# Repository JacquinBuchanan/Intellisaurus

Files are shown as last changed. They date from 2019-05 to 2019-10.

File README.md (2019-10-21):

# Intellisaurus
walking robot kit

## Assembly Videos

[Intellisaurus - Part 1 - Framing](https://www.youtube.com/watch?v=A2P9gOie0s8)

[Intellisaurus - Part 2 - Custom Cables](https://www.youtube.com/watch?v=bgMKRhBEzlM&t=16s)

[Intellisaurus - Part 3 - More Framing](https://www.youtube.com/watch?v=AXAqG9Cf0UA&t=1474s)

[Intellisaurus - Part 4 - Wiring](https://www.youtube.com/watch?v=rhYsjQ5Yf_Y)

[Intellisaurus - Part 5 - Leg Assembly](https://www.youtube.com/watch?v=X2EEQunwOJA)

[Intellisaurus - Part 6 - Shell](https://www.youtube.com/watch?v=MMXVz9HQz3Y)

[Intellisaurus - Part 7 - Installing AI Kit](https://www.youtube.com/watch?v=gh2QlOyxaBA)

## Parts List
Frame Parts Laser cut from 3mm acrylic

3D printed Leg Parts

3D printed Shell parts

1 - MG90s Servo

10 - MG966s Servos https://www.amazon.com/gp/product/B07BVR816V

Arduino Nano https://www.amazon.com/gp/product/B07G99NNXL

Servo Controller board PCA9685 https://www.amazon.com/gp/product/B07BRS249H/

Sharp Distance Sensor 10 cm ( GP2Y0D810Z0F) https://www.adafruit.com/product/1927

Battery Holder for 2 18650 https://www.amazon.com/gp/product/B06XT1DM74

5 volt @ 3 Amp Voltage Regulator (for Raspberry PI) https://www.amazon.com/gp/product/B07PLSYX9G

5 volt @ 3 Amp Voltage Regulator (for Servos) https://www.amazon.com/dp/B07QX562Z5

On/Off Switch https://www.amazon.com/gp/product/B07B9RPLZD

IR Remote control with Sensor https://www.amazon.com/gp/product/B01EE4VXS0

MPU6050 Sensor https://www.amazon.com/gp/product/B00LP25V1A

3" Speaker https://www.adafruit.com/product/1314

Raspberry Pi Zero W https://www.adafruit.com/product/3708

ReSpeaker w/ microphone Array https://www.amazon.com/gp/product/B07CXSW6LB

Raspberry Pi Camera V2 https://www.amazon.com/gp/product/B01ER2SKFS

Raspberry Pi Camera to Pi Zero Cable https://www.adafruit.com/product/3157

Groove Connector https://www.amazon.com/gp/product/B01CNZ9RJO

USB connector https://www.amazon.com/gp/product/B00OK8ELNA

Servo Label Stickers

Female to Female jumper wires https://www.amazon.com/gp/product/B07GN731BK

M2 x 25mm bolt - 2

M3 x 35mm bolt  - 1

M2 x 6mm bolt - 37 https://www.amazon.com/gp/product/B0762HR8DQ

M2 x 12 mm bolt - 33 https://www.amazon.com/gp/product/B0762K9RP5

M3 x 10mm bolt - 52 https://www.amazon.com/gp/product/B012TBMGUE

M3 Nylon nuts - 61 https://www.amazon.com/gp/product/B0129BDGW6

M2 nuts - 38 https://www.amazon.com/gp/product/B07D35C66V

M2 x 6mm Nylon hex standoffs - 10 https://www.amazon.com/gp/product/B07GCXFVB1

M3 x 50mm bolt - 6 https://www.amazon.com/gp/product/B012TE1JDG

m2 x 8mm self tapping screws - 2( to mount camera) https://www.amazon.com/gp/product/B01M0P01I5

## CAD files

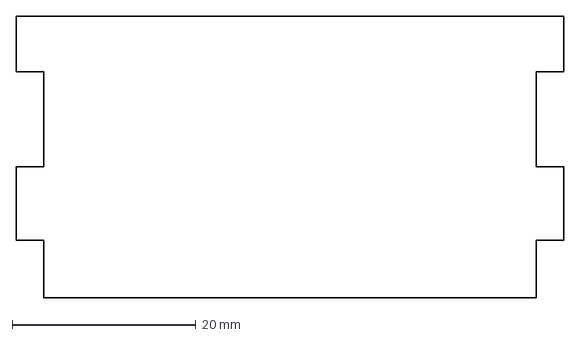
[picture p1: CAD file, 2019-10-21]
Frame DXFs/Frame Plate 9.dxf
59.6 x 30.6 mm

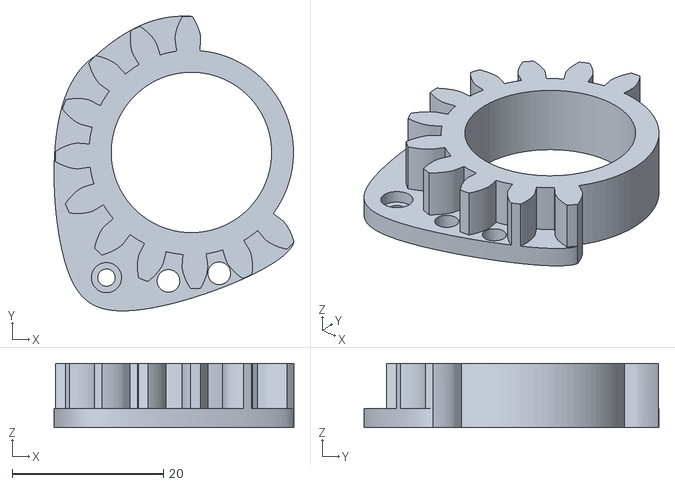
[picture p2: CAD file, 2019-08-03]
Legs STLs/FR Primary Gear.stl
31.7 x 39.0 x 8.50

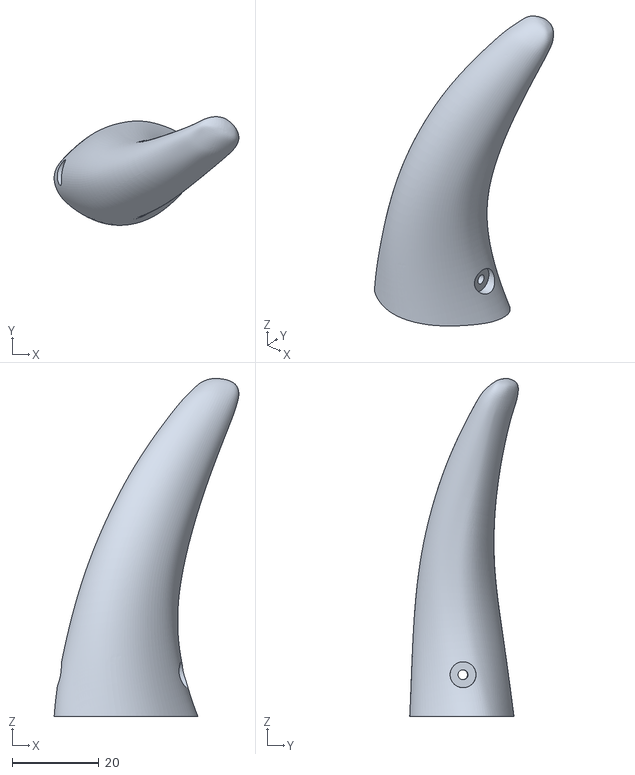
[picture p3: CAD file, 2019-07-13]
Shell STLs/Tail 3.stl
42.7 x 25.1 x 78.1

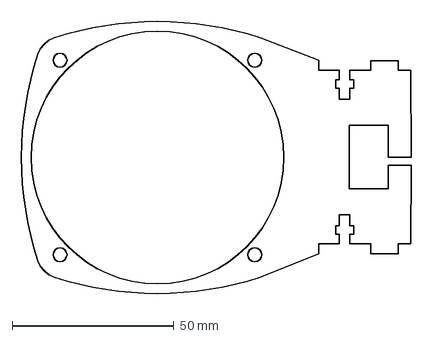
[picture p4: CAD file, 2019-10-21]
Frame DXFs/Frame Plate 4.dxf
122.0 x 87.4 mm

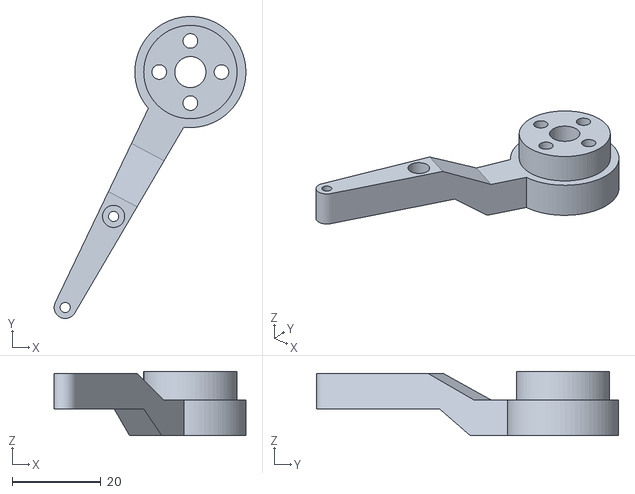
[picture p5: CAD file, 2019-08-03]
Legs STLs/FL Leg 1.stl
43.2 x 68.0 x 14.5

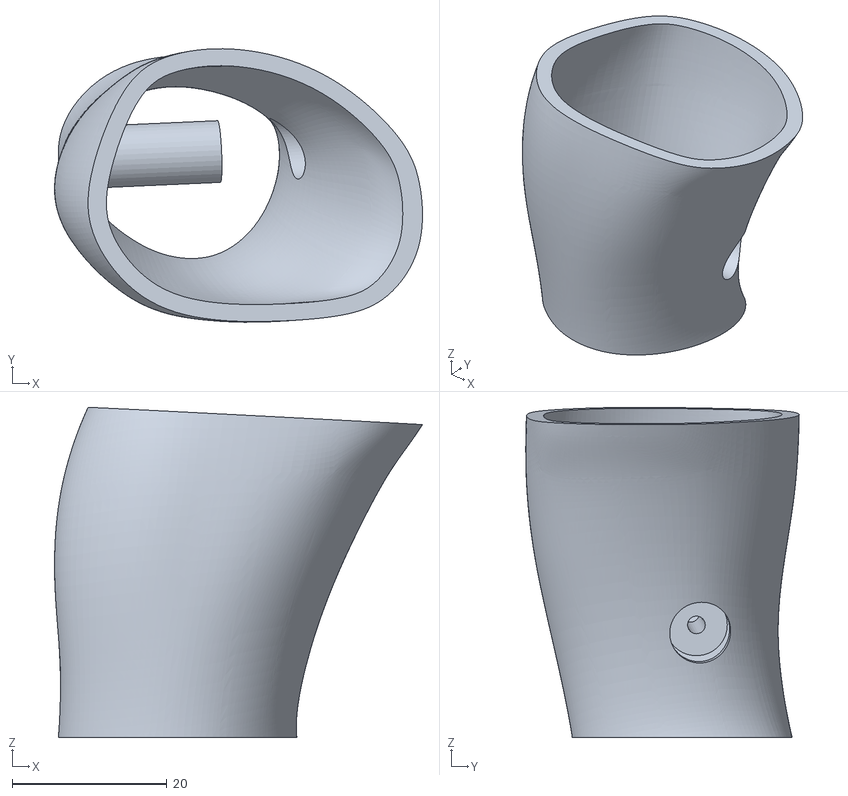
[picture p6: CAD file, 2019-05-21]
Shell STLs/BR Leg Lower.stl
47.6 x 35.4 x 42.7

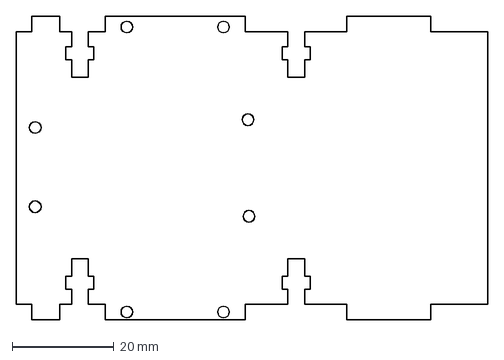
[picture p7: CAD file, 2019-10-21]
Frame DXFs/Frame Plate 5.dxf
92.7 x 59.6 mm

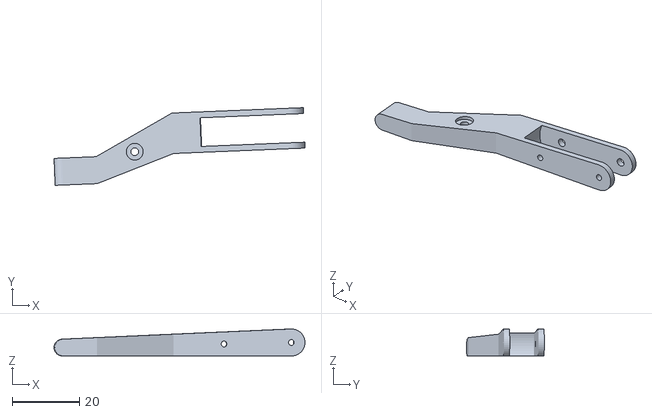
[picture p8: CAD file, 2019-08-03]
Legs STLs/FL Leg 3.stl
74.4 x 23.0 x 8.00

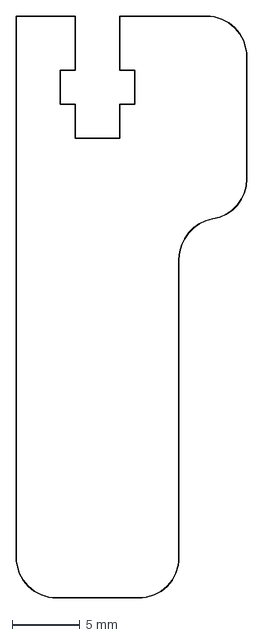
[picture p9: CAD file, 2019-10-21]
Frame DXFs/Frame Side Support.dxf
17.0 x 42.9 mm

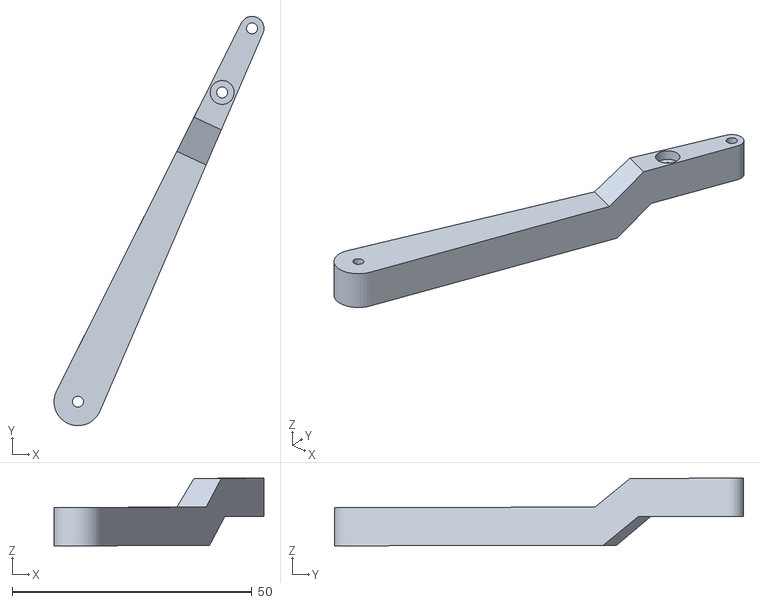
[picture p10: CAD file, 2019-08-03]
Legs STLs/BR Leg 2.stl
43.8 x 85.4 x 14.1

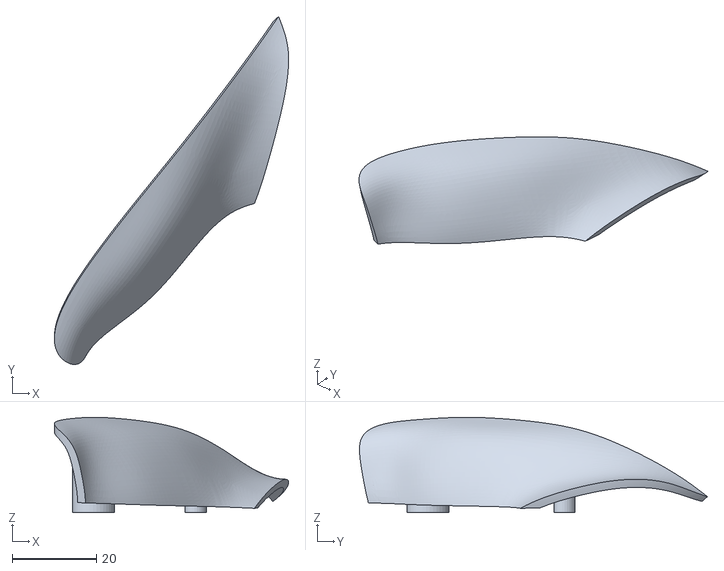
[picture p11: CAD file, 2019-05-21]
Shell STLs/FR Leg Upper 1.stl
55.7 x 82.7 x 22.6

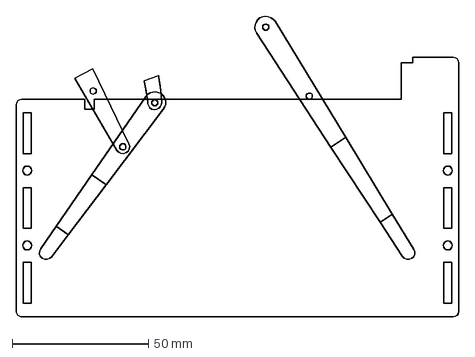
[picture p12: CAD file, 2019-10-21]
Frame DXFs/Stand Left Frame.dxf
162.7 x 110.5 mm

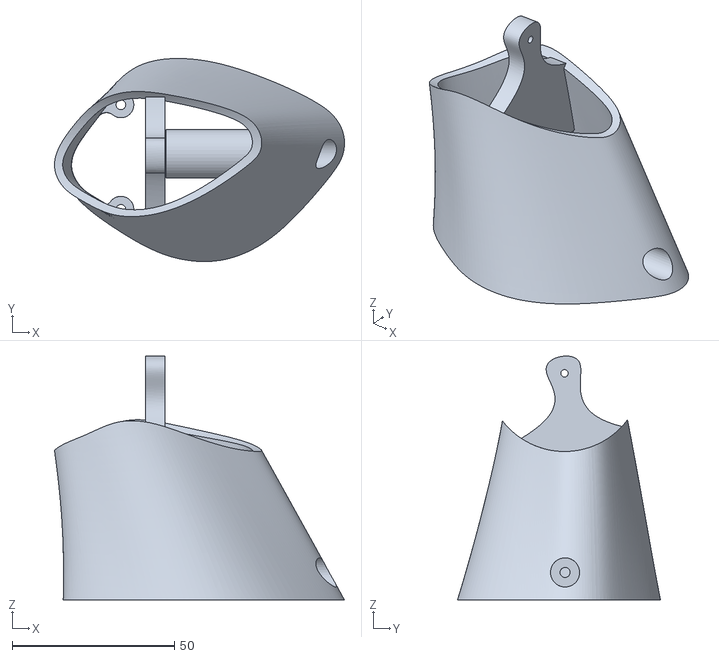
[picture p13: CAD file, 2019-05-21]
Shell STLs/Tail 1.stl
89.5 x 62.7 x 75.3

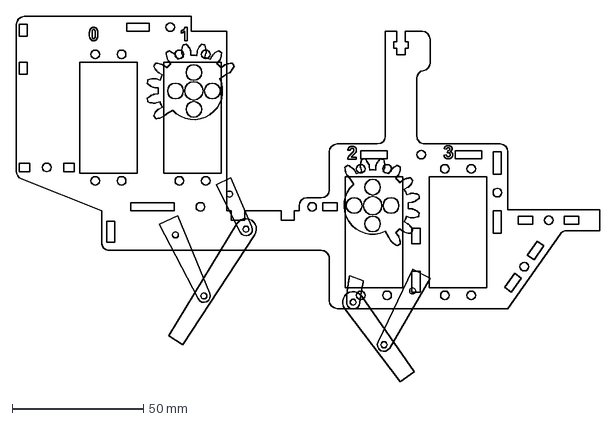
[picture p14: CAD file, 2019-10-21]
Frame DXFs/Right Body Frame.dxf
221.8 x 138.9 mm

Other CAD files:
Shell STLs/BL Leg Lower.stl
Legs STLs/BL Leg 2.stl
Legs STLs/BR Primary Gear.stl
Shell STLs/BL Leg Upper 2.stl
Frame DXFs/Frame Plate 1.dxf
Frame DXFs/Frame Plate 10.dxf
Frame DXFs/Frame Plate 2.dxf
Frame DXFs/Frame Plate 3.dxf
Frame DXFs/Frame Plate 6.dxf
Frame DXFs/Frame Plate 7.dxf
Frame DXFs/Frame Plate 8.dxf
Frame DXFs/Left Body Frame.dxf
Frame DXFs/Neck Holder Frame 2.dxf
Frame DXFs/Neck Holder Frame.dxf
Frame DXFs/Stand Cross Frame.dxf
Frame DXFs/Stand Right Frame.dxf
Legs STLs/Arduino Holder.stl
Legs STLs/BL Leg 1.stl
Legs STLs/BL Leg 3.stl
Legs STLs/BL Primary Gear 2.stl
Legs STLs/BL Primary Gear.stl
Legs STLs/BL Secondary Gear.stl
Legs STLs/BL Washer.stl
Legs STLs/BR Leg 1.stl
Legs STLs/BR Leg 3.stl
Legs STLs/BR Primary Gear 2.stl
Legs STLs/BR Secondary Gear.stl
Legs STLs/BR Washer.stl
Legs STLs/FL Leg 2.stl
Legs STLs/FL Primary Gear 2.stl
Legs STLs/FL Primary Gear.stl
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

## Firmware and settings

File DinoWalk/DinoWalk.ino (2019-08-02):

/***************************************************
     Quadropewd Walking Dinosour Robot

     copyright Jacquin Buchanan 2018
****************************************************/
#include "DinoRemoteControl.h"
#include <MPU6050_tockn.h>
#include <Wire.h>
#include <EEPROM.h>
#include <Adafruit_PWMServoDriver.h>

// called this way, it uses the default address 0x40
Adafruit_PWMServoDriver pwm = Adafruit_PWMServoDriver();
MPU6050 mpu6050(Wire);


// Define IR distance sensor model and input pin:
#define IRPin 3

// Choose the IR protocol of your remote. this isi the one shipped in the kit
CNec IRLremote;

#define MIN_PULSE_WIDTH 450
#define MAX_PULSE_WIDTH 2350
#define FREQUENCY 50

#define BACK_LEG_L1 86
#define BACK_LEG_L2 68
#define BACK_LEG_HIP_OFFSET_ANGLE  65.1
#define BACK_LEG_KNEE_OFFSET_ANGLE (-57.2)

#define FRONT_LEG_L1 60
#define FRONT_LEG_L2 48
#define FRONT_LEG_HIP_OFFSET_ANGLE  62
#define FRONT_LEG_KNEE_OFFSET_ANGLE (-64.1)

#define BACK_TO_FRONT_HIP_DIF 43.6

//These are the amount each motor gear is off from true because of the 7 degree gear size;
// these are stored in the EPROM
float MotorBuildOffsets[10] = {0.0, 0.0 , 0.0 , 0.0 , 0.0 , 0.0, 0.0, 0.0, 0.0, 0.0};
int CurrentMotorAdjusting = -1;

// The distance off the ground to hip of a normal walk
#define NORMAL_WALK_HEIGHT 98

// The distance off the ground to raise foot of a normal walk
float FootRaise[5] = {20.0, 20.0, 15.0, 10.0, 10.0};

#define MIN_FOOT_HEIGHT 70
#define MAX_FOOT_HEIGHT 100

#define MIN_FOOT_X -40
#define MAX_FOOT_X 40
#define NORMAL_STEP_LENGTH 55

#define FRONT_STEP_OFFSET_FROM_HIP_FORWARDS 0
#define BACK_STEP_OFFSET_FROM_HIP_FORWARDS 10

#define FRONT_STEP_OFFSET_FROM_HIP_BACKWARDS 15
#define BACK_STEP_OFFSET_FROM_HIP_BACKWARDS 15

int speedIndex = 0;
float StepTime[5] = {1000, 700, 500, 400, 400}; //the time for one foot step forward. (i.e. 1/4 the entire walk cycle)
float RightSideStepLength = NORMAL_STEP_LENGTH; // mm distance that each foot moves forward. NOTE this is differnt for left and right to allow turning.
float LeftSideStepLength = NORMAL_STEP_LENGTH; // mm distance that each foot moves forward. NOTE this is differnt for left and right to allow turning.

boolean leftBackwards = false;
boolean rightBackwards = false;

//four phases to a walk. One for each foot moving forward
// 0 is back right,
// 1 is front right
// 2 is back left
// 3 is front left
int walkphase = 0;

int walkPhaseIndex = 0;

int backwardsWalkPhases[4] = {1,0,3,2};

//The start time for each foots phase
unsigned long  phaseStartTime[4];
float PhaseStartFootXPos[4];
float FootXPos[4] = {0, 0, 0, 0};
float FootYPos[4] = {NORMAL_WALK_HEIGHT, NORMAL_WALK_HEIGHT, NORMAL_WALK_HEIGHT, NORMAL_WALK_HEIGHT};
boolean FootStanding[4];


//mode is used to decide what the motors are doing
// 0 is tweaking motor offsets
// 1 is standing still
// 2 is slow walking
// 3 is starting to walk, (i.e. shift weight)
// 4 is jogging
uint8_t mode;


//PID balancing variables
double last_error_LR = 0.0;
double Kp_LR = 0.02;//0.05;
double Kd_LR = 0.17;//0.17;
double K_PLR = 1.2;
double integrated_error_LR = 0.0;
double Ki_LR = 0.0001;

double last_error_FB = 0.0;
double Kp_FB = 0.02;//0.8;
double Kd_FB = 0.17;//0.27;
double K_PFB = 1.2;
double integrated_error_FB = 0.0;
double Ki_FB = 0.0001;

double GUARD_GAIN = 20.0;

float xBalanceOffset = 0.0;
float yBalanceOffset = 0.0;

#define FIRST_STEP_LEAN_ANGLE 12
#define FIRST_STEP_TAIL_ANGLE 15
#define FIRST_STEP_HEAD_ANGLE 15

float LeftRightShiftAngle[5] = {7.0, 7.0, 4.0, 3.0, 0.0};
float TailShiftAngle[5] = {15.0, 15.0, 5.0, 3.0, 0.0};
float HeadShiftAngle[5] = {7.0, 5.0, 5.0, 3.0, 0.0};


float angle0 = 90;
float angle1 = 90;
float angle2 = 90;
float angle3 = 90;
float angle4 = 90;
float angle5 = 90;
float angle6 = 90;
float angle7 = 90;


#define TAIL_WIRE 8
#define NECK_WIRE 9
#define HEAD_WIRE 10

float TailPosition = 0.0;
float NeckPosition = 0.0;
float HeadPosition = 0.0;

float TailAngle = 90;
float NeckAngle = 90;
float HeadAngle = 90;

#define TAIL_POSITION_MAX (+45)
#define TAIL_POSITION_MIN (-45)

#define NECK_POSITION_MAX  (+15)
#define NECK_POSITION_MIN  (-15)

#define HEAD_POSITION_MAX  (+12)
#define HEAD_POSITION_MIN  (-22)

char MSG_STOP_AND_STAND[] = "*** Stop and stand ";

/***************************************************
    Main Setup function

   *******************************************/
void setup() {

  Wire.begin();

  Serial.begin(9600);
  Serial.println("Walking Dinosour Robot!");

  // Servo controller setup
  pwm.begin();
  pwm.setPWMFreq(FREQUENCY);

  // Start reading the remote. PinInterrupt or PinChangeInterrupt* will automatically be selected
  if (!IRLremote.begin(IR_REMOTE_RECIVER_PIN))
    Serial.println(F("You did not choose an infrared remote input pin."));

  pinMode(IRPin, INPUT);


  //read the motor offsets from the EPROM
  if (EEPROM.read(0) == 127)
  {
    for (int i = 0; i < 10; i++) {
      MotorBuildOffsets[i] = ((float)EEPROM.read(i + 1) - 128) / 2;
      //Serial.println(MotorBuildOffsets[i]);
    }
  }

  mpu6050.begin();
  
  float gyroXoffset = 0.0;
  float gyroYoffset = 0.0;

  // the gyrooffset are stored at a specific location above the motor offsets
  if (EEPROM.read(20) == 127)
  {
    gyroXoffset = ((float)EEPROM.read(21) - 128) / 2;
    gyroYoffset = ((float)EEPROM.read(22) - 128) / 2;
  }

  // I assume these offset are based on the mounting of the devcie in the robot
  mpu6050.setGyroOffsets(gyroXoffset, gyroYoffset, 0.0);

  //Start out just standing
  mode = 1;
  CurrentMotorAdjusting = -1;
  StandPose();

}


/***************************************************
    Main Loop function

   *******************************************/
void loop() {

  mpu6050.update();
  
  // Look for some user control
  while ( RemoteControlCodeAvailable())
  {


    int inByte = RemoteControlCodeRead();
    switch (inByte)
    {

      case BUTTON_0 :
      if( mode != 0) {

        //start jogging
        //Serial.println("*** Start jogging forward ");
        
        leftBackwards = false;
        rightBackwards = false;
        mode = 4;
        unsigned long NowTime = millis();
        walkPhaseIndex = 0;
        walkphase = 0;
        speedIndex = 4;
        
        RightSideStepLength = NORMAL_STEP_LENGTH;
        LeftSideStepLength = NORMAL_STEP_LENGTH;

       for (int FootID = 0; FootID < 4; FootID++)
        {
          phaseStartTime[FootID] = NowTime;
        }
  
        
        PhaseStartFootXPos[0] = FootXPos[0];
        PhaseStartFootXPos[1] = FootXPos[1];
        PhaseStartFootXPos[2] = FootXPos[2];
        PhaseStartFootXPos[3] = FootXPos[3];
        
        break;
      }
      case BUTTON_1 :
      if (mode == 0)
        {
          CurrentMotorAdjusting = inByte - BUTTON_0;

        } else {
          TailPosition += 10;
          MoveTail();
        }
        break;
        
      case BUTTON_2 :

        if (mode == 0)
        {
          CurrentMotorAdjusting = inByte - BUTTON_0;

        } else {
          
          HeadPosition += 10;
          MoveHead();
          
        }
        break;
        
      case BUTTON_3 :
        if (mode == 0)
        {
          CurrentMotorAdjusting = inByte - BUTTON_0;


        }
        break;
        
      case BUTTON_4 :

        if (mode == 0)
        {
          CurrentMotorAdjusting = inByte - BUTTON_0;


        } else {

          
          NeckPosition += 10;
          MoveNeck();
        }
        break;
        
      case BUTTON_5 :

      if (mode == 0)
        {
          CurrentMotorAdjusting = inByte - BUTTON_0;


        } else {
          TailPosition = 0.0;
          NeckPosition = 0.0;
          HeadPosition = 0.0;
          
          MoveTail();
          MoveNeck();
          MoveHead();
        }
        break;
        
      case BUTTON_6 :
      
        if (mode == 0)
        {
          CurrentMotorAdjusting = inByte - BUTTON_0;


        } else {
          
          NeckPosition -= 10;
          MoveNeck();
        }
        break;
        
      case BUTTON_7 :
        if (mode == 0)
        {
          CurrentMotorAdjusting = inByte - BUTTON_0;


        } else {
          TailPosition -= 10;
          MoveTail();
        }
        
        break;

        case BUTTON_8 :
       if (mode == 0)
        {
          CurrentMotorAdjusting = inByte - BUTTON_0;


        } else { 
        
          
          HeadPosition -= 10;
          MoveHead();
        }
        break;

        
        case BUTTON_9 :
       if (mode == 0)
        {
          CurrentMotorAdjusting = inByte - BUTTON_0;


        }
        break;


      case BUTTON_UP:
        if (mode == 0)
        {
          if (CurrentMotorAdjusting >= 0) {
            MotorBuildOffsets[CurrentMotorAdjusting] += 0.5;

            EEPROM.write(0, 127);
            for (int i = 0; i < 10; i++)
            {
              EEPROM.write(i + 1, (byte)((int)(MotorBuildOffsets[i] * 2) + 128));
            }

            Serial.print("CurrentMotorAdjusting ");
            Serial.print(CurrentMotorAdjusting);
            Serial.print("\t v : ");
            Serial.println(MotorBuildOffsets[CurrentMotorAdjusting]);

            //Recalculate the pose to move the motor
            StandPose();
          }
        } else {

          if (mode == 2 || mode == 4) {

            if(leftBackwards && rightBackwards)
            {

              if (mode == 4)
              {
                // come out of jog and into walk
                speedIndex = 3;
                mode = 2;
                  
                
              } else {
                
              
                // We are walking backwards so slow down
                // Slow down
                speedIndex -= 1;
    
                if (speedIndex < 0)
                {
    
                  speedIndex = 0;
    
                  // Stop and stand
                  mode = 1;
                  StandPose();
    
                  Serial.println(MSG_STOP_AND_STAND);
                }
              }
              Serial.print("*** Walk backwards slower "); Serial.println(speedIndex);
              
            } else {
                // We are already walking forwards so walk faster
                speedIndex += 1;
                if (speedIndex >= 5)
                  {
                    speedIndex = 4;
                  }

                 if(speedIndex == 4)
                  {
                    //speed index 4 is a jog
                    mode = 4;
                  }
                Serial.print("*** Walk forwards faster "); Serial.println(speedIndex);

            }
              
          } else {
            // Start walking forward

            Serial.println("*** Start walking forward ");
            
            leftBackwards = false;
            rightBackwards = false;
            mode = 3;
            unsigned long NowTime = millis();
            walkPhaseIndex = 0;
            speedIndex = 0;
            phaseStartTime[0] = NowTime;

          }

          RightSideStepLength = NORMAL_STEP_LENGTH;
          LeftSideStepLength = NORMAL_STEP_LENGTH;

        }
        break;

      case BUTTON_DOWN:

        if (mode == 0)
        {
          if (CurrentMotorAdjusting >= 0) {
            MotorBuildOffsets[CurrentMotorAdjusting] -= 0.5;

            EEPROM.write(0, 127);
            for (int i = 0; i < 10; i++)
              EEPROM.write(i + 1, (byte)((int)(MotorBuildOffsets[i] * 2) + 128));

            Serial.print("CurrentMotorAdjusting ");
            Serial.print(CurrentMotorAdjusting);
            Serial.print("\t v : ");
            Serial.println(MotorBuildOffsets[CurrentMotorAdjusting]);

            //Recalculate the pose to move the motor
            StandPose();
          }
        } else {


          if (mode == 2 || mode == 4) {

            if(leftBackwards && rightBackwards)
            {
              // We are already walking backwards so speed up
                speedIndex += 1;
                if (speedIndex >= 5)
                  {
                    speedIndex = 4;
                  }

                if(speedIndex == 4)
                  {
                    //speed index 4 is a jog
                    mode = 4;
                  }
                Serial.print("*** Walk backwards faster "); Serial.println(speedIndex);
            } else {
              if (mode == 4)
              {
                // come out of jog and into walk
                speedIndex = 3;
                mode = 2;
                  
                
              } else {

                // We are walking forwards so Slow down
                speedIndex -= 1;
    
                if (speedIndex < 0) {
    
                  speedIndex = 0;
    
                  // Stop and stand
                  mode = 1;
                  StandPose();
    
                  Serial.println(MSG_STOP_AND_STAND);
                }
              }
              Serial.print("*** Walk forwads slower "); Serial.println(speedIndex);
            }
          } else {
            
              // Start walking backwards
              Serial.println("*** Start walking backwards ");
  
              mode = 3;
              unsigned long NowTime = millis();
              walkPhaseIndex = 0;
              speedIndex = 0;
              phaseStartTime[0] = NowTime;
              leftBackwards = true;
              rightBackwards = true;
            
          }

          RightSideStepLength = NORMAL_STEP_LENGTH;
          LeftSideStepLength = NORMAL_STEP_LENGTH;

        }
        break;


      case BUTTON_RIGHT:
        // Turn Right
        Serial.println("*** Turn right ");

        if (mode == 2 || mode == 3 || mode == 4) {
          if(LeftSideStepLength < NORMAL_STEP_LENGTH)
          {
            LeftSideStepLength += 10;
            LeftSideStepLength = constrain(LeftSideStepLength, 20.0 , NORMAL_STEP_LENGTH);
            RightSideStepLength = NORMAL_STEP_LENGTH;
          }else {
            RightSideStepLength -= 10;
            RightSideStepLength = constrain(RightSideStepLength, 20.0 , NORMAL_STEP_LENGTH);
            LeftSideStepLength = NORMAL_STEP_LENGTH;
          }
        } else {
            
            CurrentMotorAdjusting = -1;

            leftBackwards = false;
            rightBackwards = true;

            //very short steps for turning in place
             RightSideStepLength = 2*NORMAL_STEP_LENGTH/3;
             LeftSideStepLength = NORMAL_STEP_LENGTH;

            speedIndex = 3;
            mode = 3;
            walkPhaseIndex = 0;
            unsigned long NowTime = millis();
            for (int FootID = 0; FootID < 4; FootID++)
            {
              //This is wrong for intial step but fix it later
              phaseStartTime[FootID] = NowTime - (FootID * (StepTime[speedIndex] / 3));
            }
        }
        break;

      case BUTTON_LEFT:
        // Turn left
        Serial.println("*** Turn left ");

        if (mode == 2|| mode == 3 || mode == 4) {
          if(RightSideStepLength < NORMAL_STEP_LENGTH)
          {
              RightSideStepLength += 10;
              RightSideStepLength = constrain(RightSideStepLength, 20.0 , NORMAL_STEP_LENGTH);
              LeftSideStepLength = NORMAL_STEP_LENGTH;
          } else {
            LeftSideStepLength -= 10;
            LeftSideStepLength = constrain(LeftSideStepLength, 20.0 , NORMAL_STEP_LENGTH);
            RightSideStepLength = NORMAL_STEP_LENGTH;
          }
        } else {

            CurrentMotorAdjusting = -1;
            leftBackwards = true;
            rightBackwards = false;
            
            //very short steps for turning in place
            RightSideStepLength = NORMAL_STEP_LENGTH;
            LeftSideStepLength = 2*NORMAL_STEP_LENGTH/3;

            speedIndex = 3;

            mode = 3;
            walkPhaseIndex = 0;
            unsigned long NowTime = millis();
            for (int FootID = 0; FootID < 4; FootID++)
            {
              //This is wrong for intial step but fix it later
              phaseStartTime[FootID] = NowTime - (FootID * (StepTime[speedIndex] / 3));
            }
        }
        break;

     case BUTTON_STAR:

       if(mode == 0)
         {
            Serial.println("*** Calibrating GPU. Make sure robot is standing on flat ground. ");
            mpu6050.calcGyroOffsets(true);
  
            EEPROM.write(20, 127);
            EEPROM.write(21, (byte)((int)(mpu6050.getGyroXoffset() * 2) + 128));
            EEPROM.write(22, (byte)((int)(mpu6050.getGyroYoffset() * 2) + 128));
      
         } else {
            
            Serial.println("*** Go Straight ");
    
            if (mode == 2|| mode == 3 || mode == 4) {
              LeftSideStepLength = NORMAL_STEP_LENGTH;
              RightSideStepLength = NORMAL_STEP_LENGTH;
              
            }
       }

        break;


      case BUTTON_CENTER :
        // Stop and stand
        mode = 1;
        CurrentMotorAdjusting = -1;

        StandPose();

        Serial.println(MSG_STOP_AND_STAND);

        break;


      case BUTTON_HASH :
        // Motor setup
        mode = 0;
        CurrentMotorAdjusting = -1;

        StandPose();
        Serial.println("*** Motor Adjusting Offset Mode");
        break;

    }
  }

  if (mode == 1)
  {

    xBalanceOffset = 0.0;
    
    // Use the forward IR sensor to see if we are on ground
    int NoGround = digitalRead(IRPin);

    if(NoGround == 1)
    { 
      //We arn't on the ground so just stand straight  
      StandPose();
    } else {
      LeftRightBalance(-1, 0.0);
      FrontBackBalance(-1, -1);
    }


    FootYPos[0] = constrain(FootYPos[0], MIN_FOOT_HEIGHT , MAX_FOOT_HEIGHT);
    FootYPos[1] = constrain(FootYPos[1], MIN_FOOT_HEIGHT , MAX_FOOT_HEIGHT);
    FootYPos[2] = constrain(FootYPos[2], MIN_FOOT_HEIGHT , MAX_FOOT_HEIGHT);
    FootYPos[3] = constrain(FootYPos[3], MIN_FOOT_HEIGHT , MAX_FOOT_HEIGHT);

    
    FootXPos[0] = constrain(FootXPos[0], MIN_FOOT_X , MAX_FOOT_X);
    FootXPos[1] = constrain(FootXPos[1], MIN_FOOT_X , MAX_FOOT_X);
    FootXPos[2] = constrain(FootXPos[2], MIN_FOOT_X , MAX_FOOT_X);
    FootXPos[3] = constrain(FootXPos[3], MIN_FOOT_X , MAX_FOOT_X);

    MoveLegTo(FootXPos[0], FootYPos[0] + BACK_TO_FRONT_HIP_DIF, 0);
    MoveLegTo(FootXPos[2], FootYPos[2] + BACK_TO_FRONT_HIP_DIF, 2);
    MoveLegTo(FootXPos[1], FootYPos[1], 1);
    MoveLegTo(FootXPos[3], FootYPos[3], 3);

  }



  if (mode == 3)
  {
    //shift weight to start walking
    unsigned long NowTime = millis();

    if(NowTime > phaseStartTime[0] + StepTime[speedIndex]/2) {

      //Really Start walking
      mode = 2;
      walkPhaseIndex = 0;
      walkphase = 0;
      
      if(rightBackwards && leftBackwards)
        walkphase = backwardsWalkPhases[walkPhaseIndex];
  
      for (int FootID = 0; FootID < 4; FootID++)
      {
        //This is wrong for intial step but fix it later
        if(rightBackwards && leftBackwards)
          phaseStartTime[backwardsWalkPhases[FootID]] = NowTime - (FootID * (StepTime[speedIndex] / 3));
        else
          phaseStartTime[FootID] = NowTime - (FootID * (StepTime[speedIndex] / 3));

        FootStanding[FootID] = true;
      }
  
  
      PhaseStartFootXPos[1] = FootXPos[1] = 0;
      PhaseStartFootXPos[3] = FootXPos[3] = 0;

    if(rightBackwards || leftBackwards)
        {
          //If we are walking backwards then slide the back feet forward a little to get started
          FootXPos[0] = BACK_STEP_OFFSET_FROM_HIP_BACKWARDS*2;
          FootXPos[1] = FRONT_STEP_OFFSET_FROM_HIP_BACKWARDS;
          FootXPos[2] = BACK_STEP_OFFSET_FROM_HIP_BACKWARDS*2;
          FootXPos[3] = FRONT_STEP_OFFSET_FROM_HIP_BACKWARDS;
        }

  
    } else {

        float WeightshiftPercentage =  (float)(NowTime - (phaseStartTime[0])) / (StepTime[speedIndex]/2);
    
        WeightshiftPercentage = constrain(WeightshiftPercentage, 0.0 , 1.0);

        xBalanceOffset = GetRelativeValue( 0, FIRST_STEP_LEAN_ANGLE, WeightshiftPercentage);

        TailPosition = GetRelativeValue( 0.0, FIRST_STEP_TAIL_ANGLE, WeightshiftPercentage);
        NeckPosition = GetRelativeValue( 0.0, FIRST_STEP_HEAD_ANGLE, WeightshiftPercentage);
        MoveTail();
        MoveNeck();

        if(rightBackwards || leftBackwards)
        {
          //If we are walking backwards then slide the back feet forward a little to get started
          FootXPos[0] = GetRelativeValue( 0, BACK_STEP_OFFSET_FROM_HIP_BACKWARDS*2, WeightshiftPercentage); //RightSideStepLength / 2 + BACK_STEP_OFFSET_FROM_HIP_BACKWARDS, WeightshiftPercentage);
          FootXPos[1] = GetRelativeValue( 1, FRONT_STEP_OFFSET_FROM_HIP_BACKWARDS, WeightshiftPercentage);
          FootXPos[2] = GetRelativeValue( 2, BACK_STEP_OFFSET_FROM_HIP_BACKWARDS*2, WeightshiftPercentage); // LeftSideStepLength / 2 + BACK_STEP_OFFSET_FROM_HIP_BACKWARDS, WeightshiftPercentage);
          FootXPos[3] = GetRelativeValue( 3, FRONT_STEP_OFFSET_FROM_HIP_BACKWARDS, WeightshiftPercentage);
        }

        MoveLegsForWalk( 1.0);
    }

    //Serial.print(xBalanceOffset);Serial.print(" ***PHASE - ");Serial.println(walkphase);
  }

 // Use the forward IR sensor to see if we are about to walk off a cliff.
 int NoGround = digitalRead(IRPin);
        
 if (mode == 2 || mode == 4)
  {
    //this is a precheck for mode 2 walking forward
    if(!(rightBackwards && leftBackwards))
    {

      if( NoGround == 1) 
        {
          // Stop and stand
          mode = 1;
          CurrentMotorAdjusting = -1;
          StandPose();
          Serial.println("*** Stop and stand *** Cliff or no ground  ");
        }
       
      }
    
  }
  
  if (mode == 2)
  {
    //This is the true walking mode
    // One leg off the ground at a time.
    
    boolean HighStep = true;
    unsigned long NowTime = millis();

    unsigned long WalkPhaseExtraTime = StepTime[speedIndex]/4;
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

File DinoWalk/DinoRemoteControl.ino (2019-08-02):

#include "DinoRemoteControl.h"

boolean RemoteControlCodeAvailable()
{
  if (IRLremote.available())
    return true;

  if( Serial.available())
    return true;
  return false;
}

int  RemoteControlCodeRead()
{

  if (IRLremote.available())
  {

    // Get the new data from the IR remote
    auto data = IRLremote.read();

    switch(data.command)
    {
      case 0x19: return BUTTON_0;
      case 0x45: return BUTTON_1;
      case 0x46: return BUTTON_2;
      case 0x47: return BUTTON_3;
      case 0x44: return BUTTON_4;
      case 0x40: return BUTTON_5;
      case 0x43: return BUTTON_6;
      case 0x7: return BUTTON_7;
      case 0x15: return BUTTON_8;
      case 0x9: return BUTTON_9;
      case 0xd: return BUTTON_HASH;
      case 0x16: return BUTTON_STAR;
      case 0x18: return BUTTON_UP;
      case 0x52: return BUTTON_DOWN;
      case 0x1c: return BUTTON_CENTER;
      case 0x5a: return BUTTON_RIGHT;
      case 0x8: return BUTTON_LEFT;
    }

  }

  // Be sure the same address is used in Raspberry Pi code.
  #define RASPBERRY_PI_I2C_ADDRESS 0x13

  // Look to see if Raspberry Pi has any commands
  Wire.requestFrom(RASPBERRY_PI_I2C_ADDRESS, 6);    // request 1 byte from slave device RASPBERRY_PI_I2C_ADDRESS

  while (Wire.available()) { // slave may send less than requested
    char c = Wire.read(); // receive a byte as character
    Serial.print("FROM PI "); Serial.println(c);         // print the character
    
    switch(c)
    {
      case '0': return BUTTON_0;
      case '1': return BUTTON_1;
      case '2': return BUTTON_2;
      case '3': return BUTTON_3;
      case '4': return BUTTON_4;
      case '5': return BUTTON_5;
      case '6': return BUTTON_6;
      case '7': return BUTTON_7;
      case '8': return BUTTON_8;
      case '9': return BUTTON_9;
      case 'p': return BUTTON_HASH;
      case 'o': return BUTTON_STAR;
      case 'w': return BUTTON_UP;
      case 'x': return BUTTON_DOWN;
      case 's': return BUTTON_CENTER;
      case 'd': return BUTTON_RIGHT;
      case 'a': return BUTTON_LEFT;
    }
    
  }

  // this is the serial debug port in Arduino IDE
  if ( Serial.available())
  {
    int inByte = Serial.read();

    switch(inByte)
    {
      case '0': return BUTTON_0;
      case '1': return BUTTON_1;
      case '2': return BUTTON_2;
      case '3': return BUTTON_3;
      case '4': return BUTTON_4;
      case '5': return BUTTON_5;
      case '6': return BUTTON_6;
      case '7': return BUTTON_7;
      case '8': return BUTTON_8;
      case '9': return BUTTON_9;
      case 'p': return BUTTON_HASH;
      case 'o': return BUTTON_STAR;
      case 'w': return BUTTON_UP;
      case 'x': return BUTTON_DOWN;
      case 's': return BUTTON_CENTER;
      case 'd': return BUTTON_RIGHT;
      case 'a': return BUTTON_LEFT;
    }
  }
  return 0;
}

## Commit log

2019-05-21 Initial Add of 3D printable Parts
    Initial Add of the 3D printable parts for the Legs and outer shell.
    [Arduino Holder.stl, BL Leg 1.stl, BL Leg 2.stl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]
2019-07-01 Washers were too small
    [BL Washer.stl, BR Washer.stl, FL Washer.stl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]
2019-07-01 Add SVG files for laser cut frame
    Intended to laser cut 1/8 inch or 3mm acrylic
2019-07-13 tweaks to frame
2019-07-13 Tweaks to Shell Head and Tail End
    [Tail 3.stl]
2019-07-23 Added a USB right angle cover
    [USB Right Angle Cover.stl]
2019-08-02 Added IR Range Sensor Holder
    [Range Sensor Holder.stl]
2019-08-02 Added Arduino Code
2019-08-03 Added Embossed Left-Right labels to leg parts
    [BL Leg 1.stl, BL Leg 2.stl, BL Leg 3.stl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]
2019-10-21 Added assembly instructions and parts list
2019-10-21 Added DXF versions of Frame parts
    [Frame Plate 1.dxf, Frame Plate 10.dxf, Frame Plate 2.dxf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]
